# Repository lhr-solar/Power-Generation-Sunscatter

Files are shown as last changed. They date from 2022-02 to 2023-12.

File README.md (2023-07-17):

# :sunny: Sunscatter - Maximum Power Point Tracker Board

- [:sunny: Sunscatter - Maximum Power Point Tracker Board](#sunny-sunscatter---maximum-power-point-tracker-board)
  - [Repository Structure](#repository-structure)
  - [Maintainers](#maintainers)
  - [Versioning](#versioning)
  - [TODO](#todo)

---

## Repository Structure

- **datasheets** - contains datasheets for major components of the Sunscatter.
- **docs** - contains documentation on how to build, test, and use the Sunscatter.
- **fw** - contains fw that is loaded onto the Sunscatter.
  - **tests** - test programs used to characterize and validate the Sunscatter.
  - **src** - main program used to run the Sunscatter.
  - **inc** - internally developed libraries specific for the Sunscatter.
  - **lib** - third party libraries used by the Sunscatter.
- **hw**
  - **Footprints** - project specfic footprint association files for the Sunscatter.
  - **Models** - 3d .step files for the PCB 3d viewer.
  - **Symbols** - project specific symbol files for the Sunscatter.
  - **vX_Y_Z** - frozen versioning folder for PCB production files.
  - design files

---

## Maintainers

The current maintainer of this project is Matthew Yu as of 07/16/2023. His email
is [matthewjkyu@gmail.com](matthewjkyu@gmail.com).

Contributors to the HW and FW encompass many dedicated students, including:

- Jacob Pustilnik
- Afnan Mir
- Youssef Elsherif
- Austin Tsao
- Joseph Onofre
- Ricky Tiet
- Javier Lopez
- Chioma Okorie
- Corey Hulse
- Kaleb Todd
- Jennifer Dahm
- And many others...

Special thanks to Professor Gary Hallock, who supervised the development and
design of this project.

---

## Versioning

This PCB is on unified version `3.4.0`. Every time the schematic and/or layout
is updated, this version number should go up. We use [semantic
versioning](https://semver.org/) to denote between versions. See the
[changelog](./docs/CHANGELOG.md) for more details.

---

## TODO

Documentation

- Update assembly and testing document, ordering document, and improvement document.
- Add datasheets for key components of the device.

HW

- Transition to v4.0.0 using modified board design from MPPT-design repo
- Clean up files in hw folder

SW

- Regenerate code for MBED with proposed filestructure

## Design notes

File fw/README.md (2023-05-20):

# Sunscatter Firmware

This repository contains all relevant firmware and documentation files for the
Sunscatter MPPT FW.

A couple other important sections for programmers who are working with this
board are below. 

- [Repository Structure](#Repository-Structure)
- [Maintainers](#Maintainers)
- [Versioning](#Versioning)
- [Changes and Errata](#Changes-and-Errata)
- [List of TODOs](#TODO)

---

## Repository Structure
- **inc**: Includes additional files and libraries made by external sources,
  like MBED from ARM.
- **lib**: Includes additional files and libraries developed by internal sources.
- **src**: Includes all projects, including test programs. The main program is
  typicalnamed after the root directory name. E.g. Sunscatter.
- **documentation**: Contains documentation for building, flashing, testing, and
  characterizing the HW.
  - [IMPROVEMENT.md](documentation/IMPROVEMENT.md): Suggestions for improving
    the software, libraries, and/or tests.
  - [BUILDING.md](documentation/BUILDING.md): Instructions for installing all
    prerequisites and building the program. Also how to flash onto the board.
  - [TESTING.md](documentation/TESTING.md): Instructions for testing the board
    hardware (past the basic electrical tests found in
    pcb/documentation/ASSEMBLY_AND_TESTING.md) and characterizing the hardware. 

---

## Maintainers

The current maintainer of this project is Matthew Yu as of 07/15/2022. His email
is [matthewjkyu@gmail.com](matthewjkyu@gmail.com). 

Also a useful point of contact is Professor Gary Hallock, who advised Matthew
and worked with the several former senior design teams and solar car class
groups who developed this board.

Other contributors of this FW are as follows:
- Afnan Mir (v0.1.0)
- Roy Moore (v0.1.0)
- Gary Hallock (v0.1.0)
- And many others...

---

## Versioning

Each FW program has an internal version number located at the header. The
current FW version of the main program, `MPPT` is `0.1.0`. It is still in beta.
We use [semantic versioning](https://semver.org/) to denote between versions.

---

## Changes and Errata

### Release 0.1.0

- Initial formatting of the repository structure
- Added the following tests:
  - boost_characterization_test
  - can_test
  - indicator_test
  - sensor_test
  - step_response_test
  - voltage_sweep_mppt_test
- Added main program Sunscatter.
- Versioning for each test based on hardware revision.

---

## TODO
- [#1. Figure out switching node requirements on overshoot and ringing.](https://github.com/lhr-solar/Power-Generation/issues/1) 
- Add libraries for Sunscatter program.
- Update Sunscatter program to use on MPPT.
- Clean up Boost Characterization Test.

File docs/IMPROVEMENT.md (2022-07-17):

# IMPROVEMENTS FOR SUNSCATTER HW

v1.0.0

This is a list of changes we can make to the board in future versions to improve
it in various ways. Some of these are functional, others are purely aesthetic.

1. **Isolate Nucleo From High-Power Domain**

   Currently, the Nucleo operates in the same power domain (that is, the same
   ground and without isolation) as the high power components of the board -
   that is, the DC/DC boost converter. It would be far safer for it to be
   isolated, both for the Nucleo itself and for users interacting with it.

   Once the Nucleo is properly isolated from the high-power domain, it can
   either be tied directly to the car's low-power domain, or it can remain
   isolated from it. For simplicity I recommend tying it to the car's low-power
   domain, but it might be slightly safer for operators if it's isolated.

   Three major components would need to be reworked to enable this:
   1. the voltage sensors
   2. the current sensors
   3. the MOSFET driver

   These are the next couple of numbered points.

2. **Upgrading the voltage sensors**

   To upgrade the voltage sensors, we would want to use an isolating amplifier
   such as the AMC1211. This chip has an input range of 0-2V, so we would need
   to adjust the voltage dividers and their protection diodes appropriately.
   Both the input and the output require 3.3-5V power.

   The output of TI's isolating amplifiers, unfortunately, is differential
   rather than single-sided. (Explain how to convert this. example in
   datasheet. Idea: difference amplifier like INA132?)

3. **Upgrading the current sensors**

   Just like voltage sensors, but with current-sense isolating amplifiers.

4. **Upgrading the MOSFET driver**

   This is a fairly easy upgrade, since our current chip already looks a lot
   like an isolated FET driver.

   TI designs chips specifically for driving MOSFETs through isolation. One
   example of this is the UCC21541, with dual-channel isolation.* On the
   input/Nucleo side, you would provide 3.3V power from the Nucleo and use
   standard IO to drive IN_A. On the output side, you would provide 12V from the
   high-power domain and route the output just like you would from our current
   chip.

   As of this writing, the price for the UCC21541 is similar to that of our
   current chip, but Mouser currently doesn't stock it. We would want to find
   one that operates similarly but that Mouser actually stocks.

   We only need one channel, but the only chips TI offers with one-channel
   isolation are far more complicated to use.

5. **Switch to synchronous boost converter**

   Up to 8A * 1.75V = 14W may be dissipated through the schottky diode forward
   bias mode. Perhaps higher based on surge current. This loss can be reduced by
   replacing the schottky diodes with low Rds_ON mosfets. This may also reduce
   the need for a third heatsink.

   Note that the noise should proportionally double. We should test combinations
   of the boost converter with the snubber circuit to see if the power loss
   through the snubber is more significant than the power saved using a
   synchronous topology.

6. **Add ports for light and temperature sensors**

    Merging the Blackbody boards with Sunscatter can reduce board waste for
    minimal space utilization. Required: 2 TSL2591 or equivalent light sensing
    ports, and up to 8 RTD sensors. The latter may use a multiplexer and a
    single MAX31865 chip. Test w/ v2.0.0 of Blackbody A first.

7. **Upgrade MCU processor and use just the chip**

    Currently we use the nucleo breakout board. Other LHR Solar boards solder
    the STM32L432KC chip directly to the PCB. This reduces space and removes
    extra peripherals that are not used. Requires extra hardware for STLINK
    communication and flashing.

8. **Reset switch Pullup**

    Powering the Nucleo through 5V (using Car Power 12V instead of the 9V supply
    for testing) needs a pullup resistor on the reset switch (SW101). Behavior
    is finnicky and the Nucleo onboard pullup is insufficient.

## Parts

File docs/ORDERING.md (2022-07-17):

# HOW TO ORDER THIS PCB

v1.1.0

Ordering the board will vary from distributor to distributor; some will take the
KiCAD project directly, others require Gerber files. If they require gerber
files, some will require specific naming conventions for each layer.

## Ordering Instructions: JLCPCB

Our preferred manufacturer (or at least mine) of choice is JLCPCB. They
manufacture hobby boards cheaply and quickly, and at relatively high quality
compared to other fab houses.

JLCPCB will manufacture 5 PCBs for 2$ (sans shipping and handling) if the PCBs
are <= 100mm * 100mm. They also have an SMD assembly surface where one side of
the PCB is populated, often for very cheap prices compared to the amount of
labor you would have to put in to solder all the components on.

For this PCB (Sunscatter), we will order from JLCPCB and also do SMD assembly
from them. KiCAD has nice, open source extensions that can quickly create build
files that JLCPCB will accept for manufacturing and assembly.

### Preparing the Gerbers

First make sure that the JLCPCB plugin is installed via the Plugin and Content
Manager.

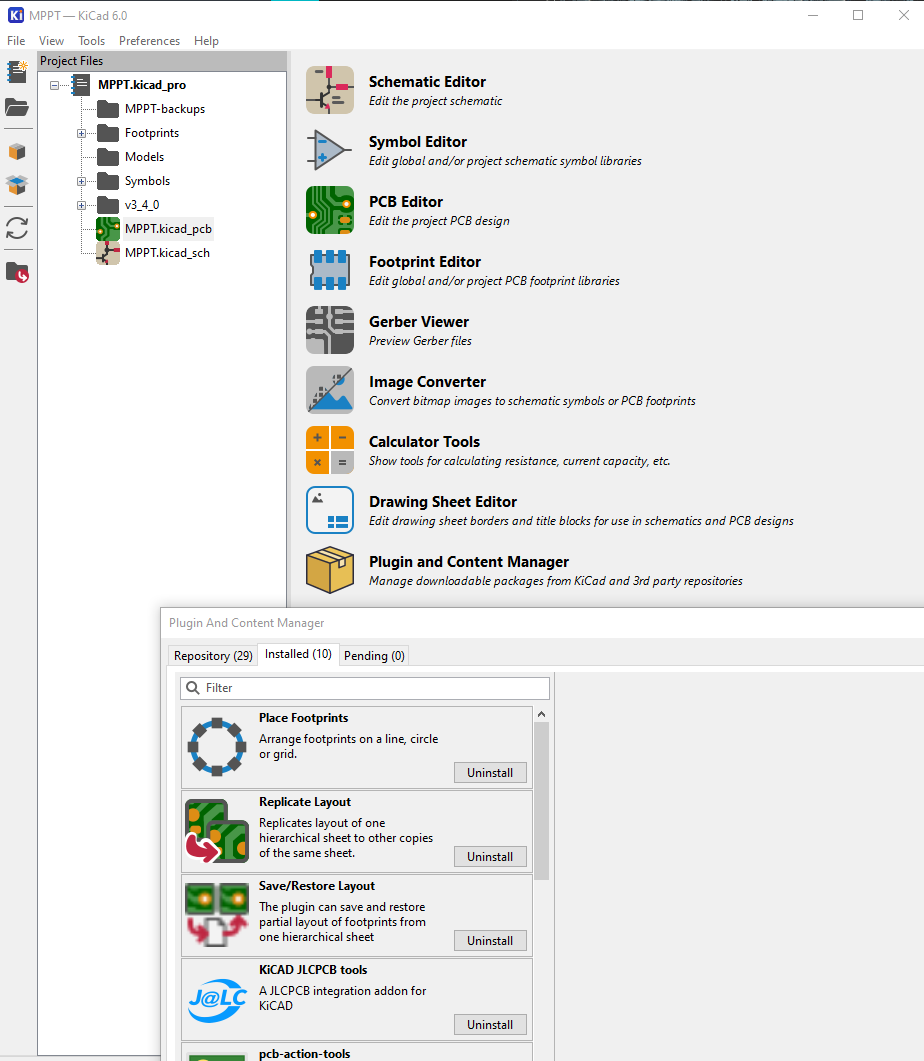
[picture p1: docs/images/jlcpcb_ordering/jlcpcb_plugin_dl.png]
Install plugin


Then make sure your schematic symbol table has following columns populated for
each component:
- Value
- Reference
- Footprint
- JLCPCB BOM
- LCSC Part

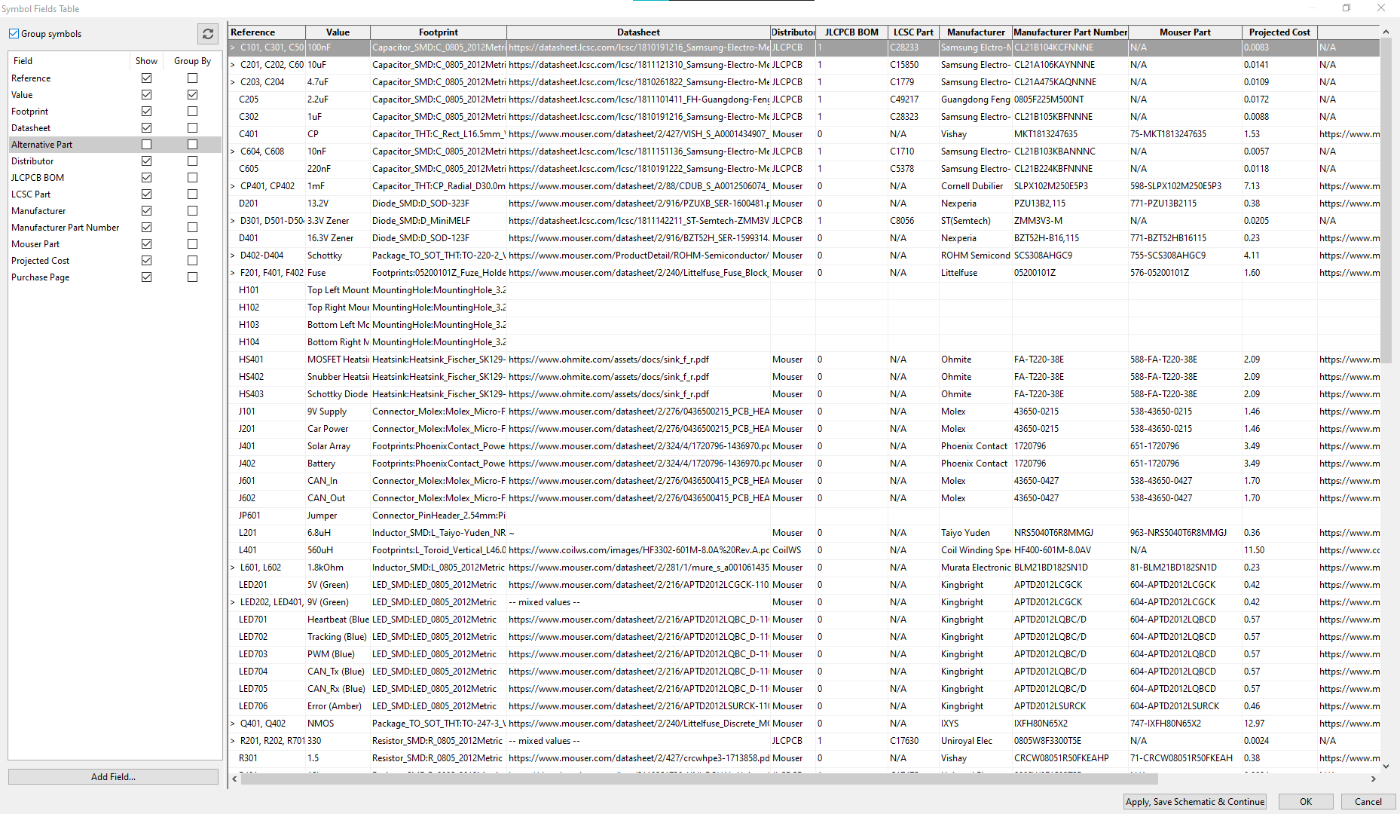
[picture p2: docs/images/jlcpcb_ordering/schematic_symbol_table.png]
Populated symbol table


Go to the PCB editor, and after the layout finishes and everything passes DRC
click on the JLCPCB button.

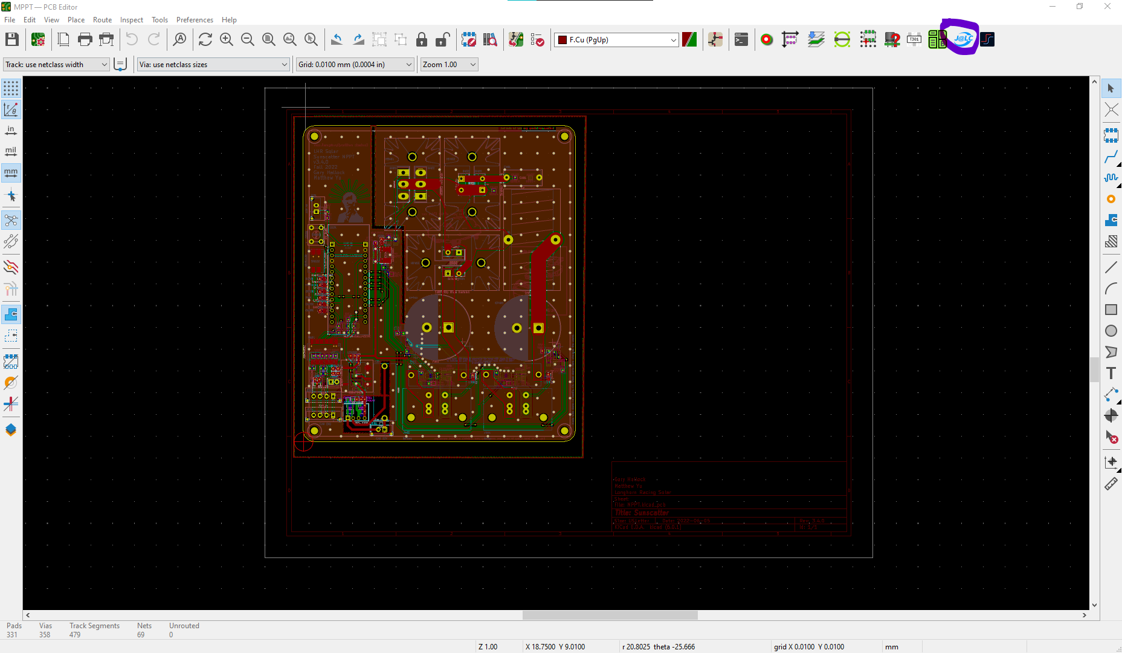
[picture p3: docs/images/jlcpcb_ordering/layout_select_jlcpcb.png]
JLCPCB buttom


Finally generate the fab files using the Generate Fabrication Files button. Make
sure the BOM and POS have a checkmark for all components you want assembled by JLCPCB.

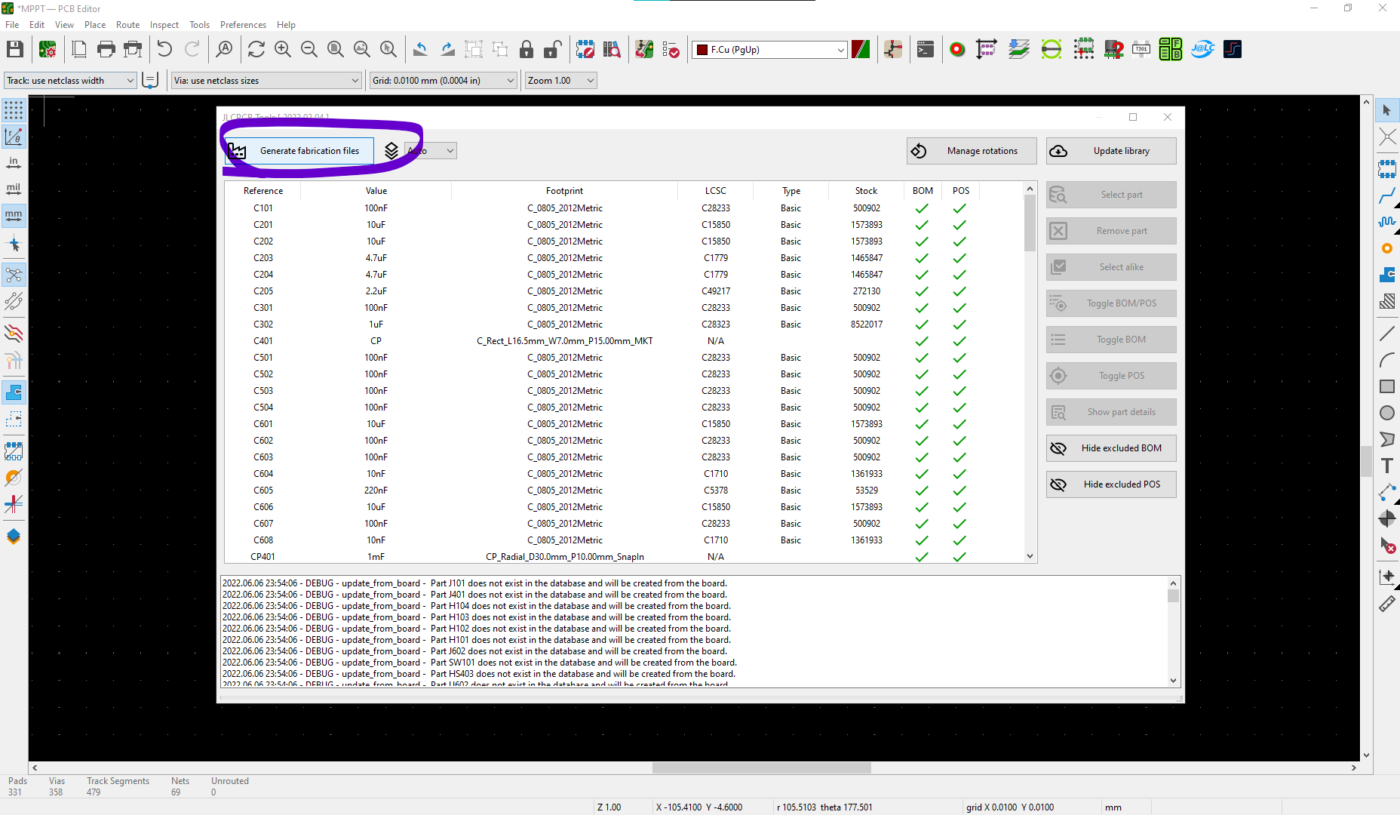
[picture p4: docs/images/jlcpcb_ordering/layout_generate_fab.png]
Generate gerbers


### Ordering from JLCPCB

After the gerbers are generated properly, head onto the JLCPCB
[site](jlcpcb.com).

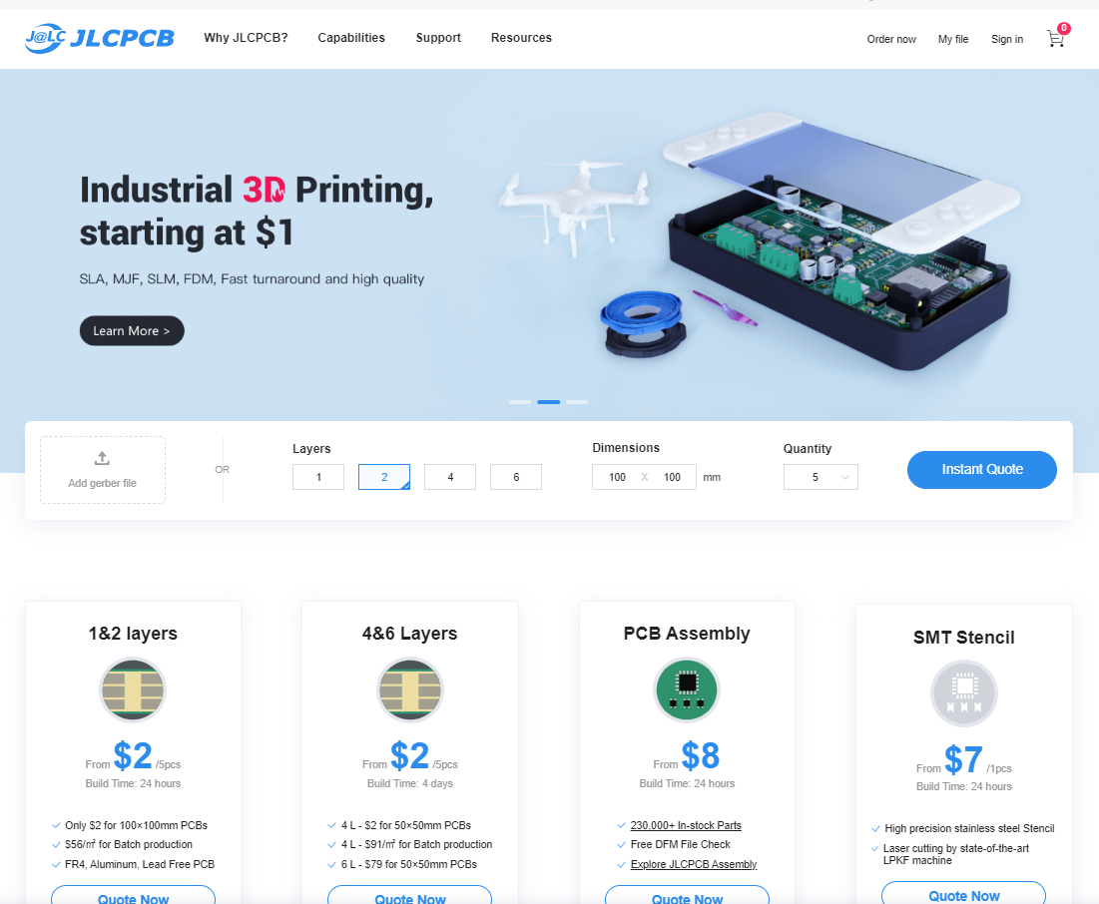
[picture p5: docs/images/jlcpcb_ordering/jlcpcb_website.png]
JLCPCB site


Go and get a quote.

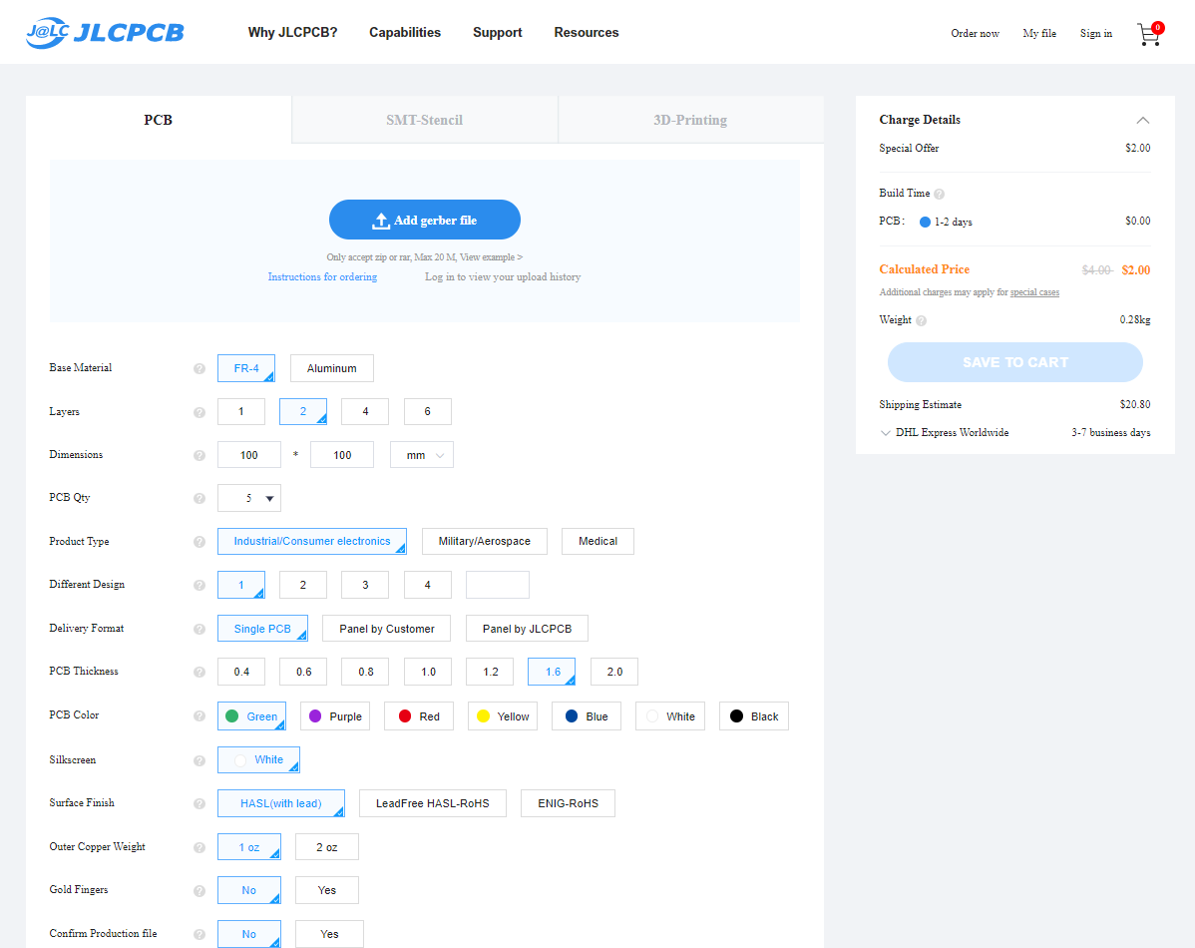
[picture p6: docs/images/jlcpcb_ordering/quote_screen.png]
JLCPCB quote


If you press the add gerber file button, you can upload the output gerber files.
They are found in the `jlcpcb/assembly/gerber` folder as `GERBER-xxx.zip`.

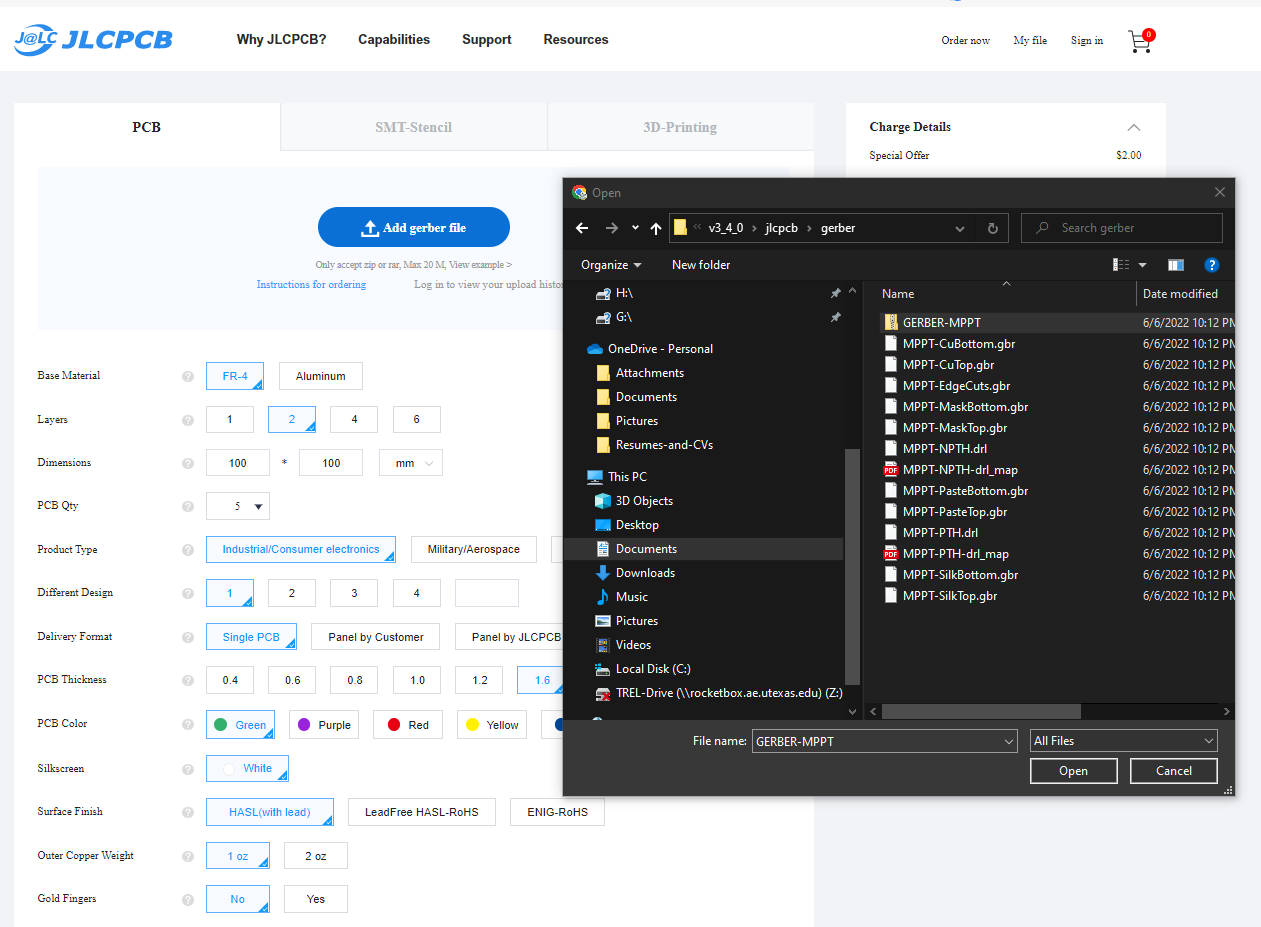
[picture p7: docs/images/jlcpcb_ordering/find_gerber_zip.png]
Adding gerbers


The webpage will load the gerbers, if they are in the correct format and board
passes some checks it'll show up. The dimensions of the board will be updated
and a new quote price will be displayed.

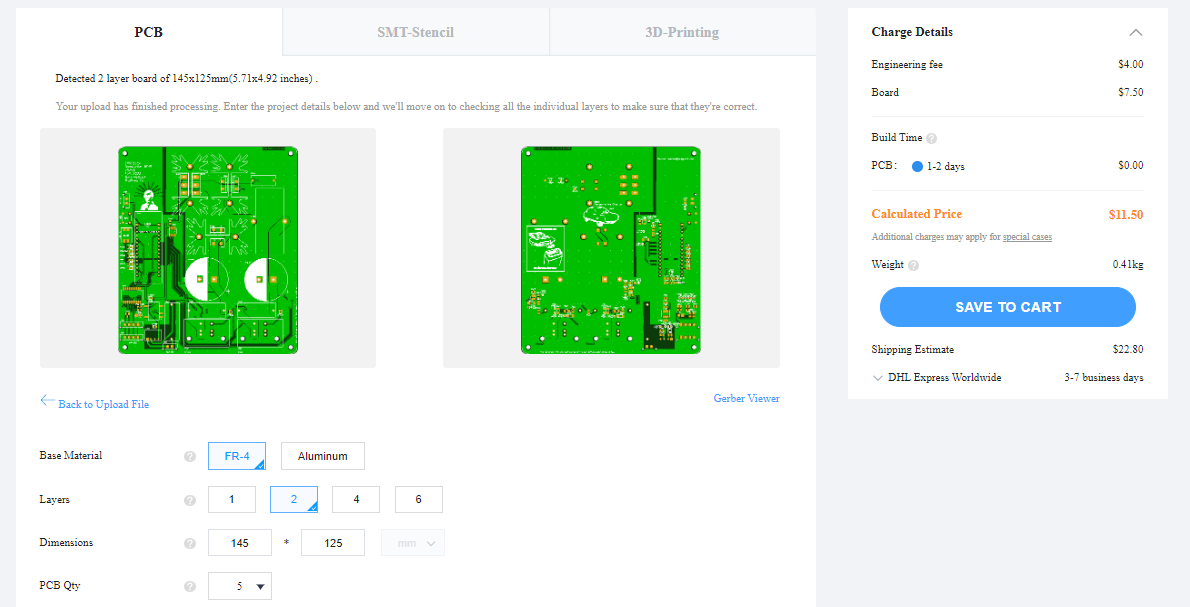
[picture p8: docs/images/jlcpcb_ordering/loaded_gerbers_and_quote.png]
New quote


We can then go down the screen and enable the PCB assembly option. We can choose
which side we want to assemble and the number of boards to assemble (2 or 5).

Assembly option

The next page after hitting confirm asks for a BOM and CPL file, the latter is
the position of the components to be assembled on the board. We can find those
as `jlcpcb/assembly/BOM-xxx.csv` and `jlcpcb/assembly/POS-xxx.csv` respectively.

Assembly file input

The next page will load the BOM and check against the LCSC internal database and
match all available components. We prefer basic components since every extended
component is an extra 2$ fee per type to manually load.

BOM matching

The next page reviews the PCB, you can zoom in on the screen to see where each
component will be placed. Make sure it matches or the engineer who inspects the
files will send an email back with complaints and the order will be delayed.

Review
Zoomed in

Finally you can save the order to the cart, review everything, and order it.
Feel free to select the delivery system that best fits your timeline and the
budget, and use any coupons if you have any.

Shopping Cart

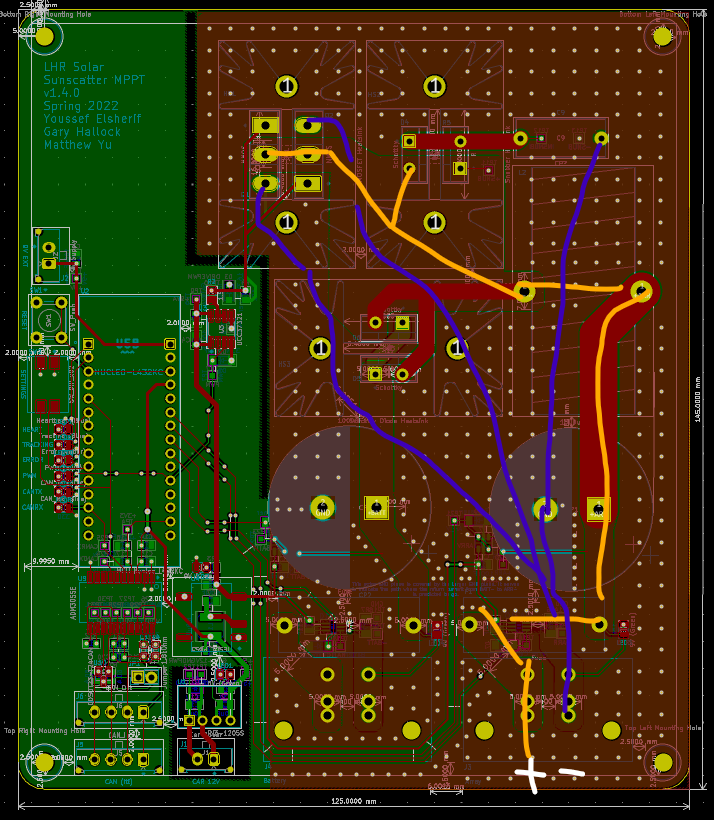
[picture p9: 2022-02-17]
docs/images/jlcpcb_ordering/GateON.png

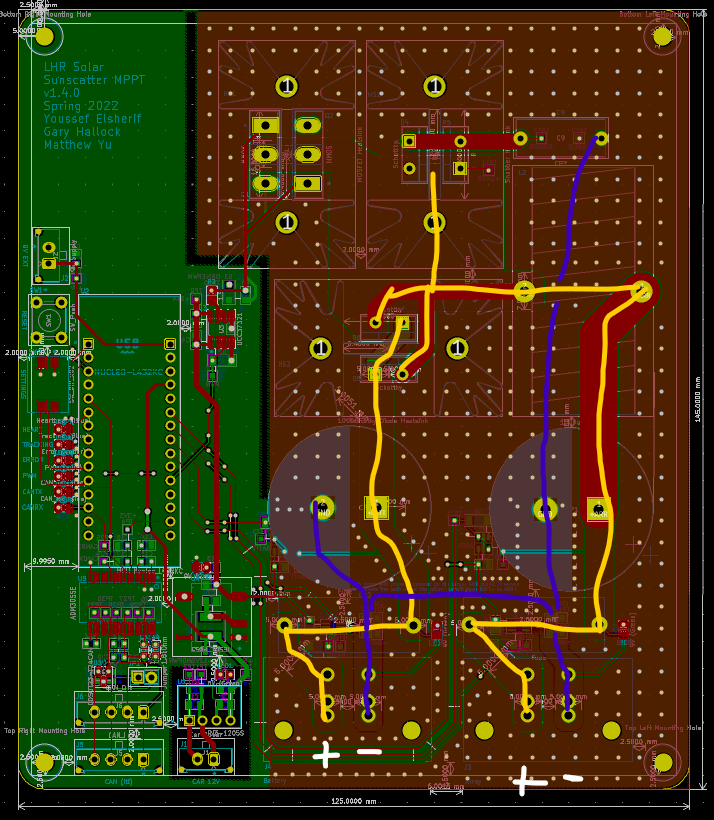
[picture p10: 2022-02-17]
docs/images/jlcpcb_ordering/GateOFF.png

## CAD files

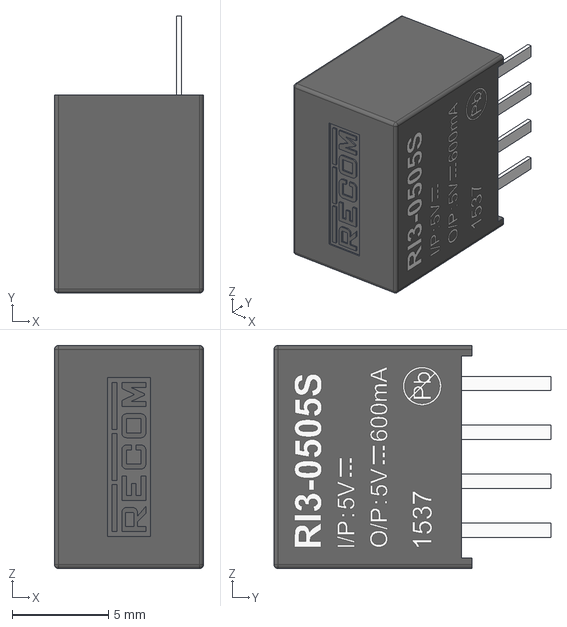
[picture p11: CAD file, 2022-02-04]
hw/Models/RI3-1205S.step
7.75 x 14.4 x 11.6 mm

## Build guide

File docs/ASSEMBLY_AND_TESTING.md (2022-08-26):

# HOW TO ASSEMBLE AND ELECTRICALLY TEST THIS PCB

v1.1.0

## Assembly and Testing Instructions

### v3.2.0

The board should be assembled and tested in sections to ensure proper
functioning. Assembly should go through the following sections in order:

1. Power Regulation
2. LEDs
3. Nucleo Connections
4. Sensors (Voltage and Current)
5. CAN
6. DC/DC Converter

#### Step by Step Instructions

It's highly recommended to pull up the schematic and layout side by side while
assembling and testing the board. As a tip, you can click on the schematic
symbol, and if the layout window is open, it'll jump to that part on the layout.
Also hide everything except the Silkscreen or Fabrication layer (of the right
side of the PCB) to remove any clutter from the layout.

Also, if you find any discrepancies between these instructions and the board
layout, please file a PR or issue so it can be fixed!

1. Initial Board Checks

   Before installing anything, check for power shorts where there shouldn't be:
   - Between Array + and -
   - Between Battery + and -
   - Between Array and Battery
   - Between Car Power +12V and GNDPWR
   - Between Device Power +9VA and GNDREF
   - Between Car Power +12V and Device Power +9VA
   - Between Car Power GNDPWR and Device Power GNDREF
   - Between CAN Iso Vout and GndOut
   - Between CAN Iso Vin and GndIn
   - Between CAN Iso Vout and Vin
   - Between CAN Iso GndOut and GndIn

   Other important shorts to check for and eliminate:
   - Between CAN H and L
   - Between MOSFET terminals
   - Between Schottky Diode terminals
   - Between heat sinks and ground
   - On each Nucleo board, between A4 and D4 (shorted by SB18)
   - On each Nucleo board, between A5 and D5 (shorted by SB16)

2. Assembling Power Regulation

   1. Solder the smallest components first: L1, C4, C5, C6, C7. These can be
      done in any order.
   2. Solder test points: TP5, TP6, TP7, TP8. These can be done in any order.
   3. Solder power regulator U3.
   4. Solder the connector J1.
   5. Test for the following shorts:
      - Between Car Power +12V and GNDPWR.
      - Between Device Power +9VA and GNDREF.
      - Between Car Power +12V and Device Power +9VA.
      - Between Car Power GNDPWR and Device Power GNDREF.
      - Between pins on U3
   6. Connect +12V to the connector and verify that +9VA is at TP7.
   7. As a bonus, somehow make some noise at +12V and see how stable +9VA is.

3. LEDs

   1. Solder the smallest components first: R2 - R11 and LED1 - LED10. You get
      the drill by now.
   2. Check for shorts across each resistor-LED pair. As a tip, the LED
      reference number is always one less than the resistor reference number.
   3. Further testing on these will occur in the next step.

4. Nucleo Connections

   1. Solder the smallest components first: D1, D2, C1, C2, C3, R1. Make sure
      you know which direction the diodes should go on the layout. You get the
      drill by now.
   2. Solder test points: TP1, TP2, TP3, TP4.
   3. Solder the Drive PWM signal driver U2.
   4. Solder the headers for the Nucleo (U1) and make sure they are upright.
   5. Then solder in the switches SW1 and SW2.
   6. Test for the following shorts:
      - Across SW1 (shorts only when pushed)
      - Across SW2 (shorts only when ON)
      - Between pins on U2 (and U1, if you're bored)
   7. Plug in the Nucleo and then test for shorts between D4 and A4 and between
      D5 and A5. If there are shorts here, you will need to remove SB18 or SB16,
      respectively, from the Nucleo board.

      **YOU MUST DO THIS FOR EVERY NUCLEO YOU PLUG INTO THE MPPT.**

   8. Load up the Nucelo with a test program to cycle LED pins and outputs a PWM
      signal with a non-trivial duty cycle and see if they light up/are correct
      on an O-scope. Unplug the Nucleo from USB, and connect 12V to the Car
      Power Connector J1 (But not both!). Make sure the Nucleo powers on again
      and the test program works as expected.
   9. Remove the Nucleo and all sources of power before further assembly.

5. Sensors (Voltage and Current Sensors)

   It's recommended to do one of these sensors at a time.

   1. Pick a sensor. We'll use the Array Voltage Sensor as an example.
   2. Solder the smallest components first: R18, R19, R20, C15, D11, D12. Make
      sure you know which direction the diodes should go on the layout.
   3. Solder test point TP19.
   4. Solder the chip U6.
   5. Test for shorts across the pins on U6, and that we have a connection
      between pad 6 of U6 (+3.3V) and the +3.3V pin of the Nucleo (after
      plugging it in, but not powering it).
   6. To test the sensor, you can now power the Nucleo with the USB.
      Apply a large voltage across Array +/- (likewise with Battery +/-). The
      LED circuitry for the array is designed for up to 100V, and the LED circuitry
      for the battery is designed for up to 130V.

      Note: If you're starting with the voltage sensors, you'll need to bridge
      Arr- or Batt- with GNDPWR first until the current sensors are installed.
      You could probably do a solder bridge on the current sensor shunt
      resistor, but if you're uncomfortable removing solder there later, use
      some thick wire to bridge the test points for ARR- (TP12) and BATT- (TP16)
      with the GNDREF test point (TP8). You could also use -SNUB (TP15) as
      GNDREF.

      Make sure you can read the expected voltage or voltage range at the output
      test points. You might also want to run a profile across the sensors and
      profile the relationship for interfacing the sensors in SW later. At
      least, it'll make your life easier in the future.

      Make sure you remove the Nucleo and any power after testing.

6. CAN Circuit

   1. Solder chip U8 **first** and test for shorts across adjacent pins.
   2. Solder the smallest components: C17 - C24, L3, L4, R25, R26.
   3. Solder bridge R24.
   4. Solder test points TP21 - TP28.
   5. Solder the chip U9.
   6. Solder the termination header JP1.
   7. Solder the CAN Connectors J4, J5.
   8. Test for the following shorts:
      - Between CAN_H and CAN_L.
      - Between CAN_Tx, CAN_Rx.
      - +5V and GNDPWR (Power side).
      - 5V and GND (CAN side).
      - Across adjacent pins in U8, U9.
   9. Plug in the Nucleo, connect J4/J5 to a CAN bus, and run a CAN
      communication test to ensure that the installed CAN circuitry is
      functional.
   10. Remove any power, the Nucleo, and then CAN connections before further
       assembly.

7. DC-DC Converter
   1. Solder the smallest components first: D3, R12. Make sure you know which
      direction the diodes should go on the layout.
   2. Then do some of the larger parts, in no particular order: F1, F2, R13, C9.
   3. Now install the heatsinks HS1 - HS3.
   4. Then install the MOSFETs and other diodes: Q1, Q2, D4, D5, D6. Make sure
      they fit the heatsinks and have a screw inserted to keep them connected.
      Maybe add thermal paste.
   5. Install the test points: TP9 - TP16.
   6. Finally, install the large stuff: J2, J3, C8, C9, L2.

8. Post checks

   Now that you've made it to the end (we hope) of assembly and preliminary
   testing, you should do a couple things before running full MPPT tests and
   running MPPT algorithms on it.

   1. First, check the board for obvious soldering defections like burnt traces
      or exposed component legs. Make sure those still work. For any solder
      bridges that shouldn't fix, you should fix them. Or get somebody who's
      better than you to fix them.
   2. Check to see if you have any remaining parts hiding in the pile of
      plastic packages you probably received. Any remaining parts should
      probably be a cause for concern (unless you knew you were going to blow
      something and had the foresight to get extra) and you should definitely
      see where they might have come from.

      The MPPT Parts list is **THE** definite source of truth, and tells you
      where each part is tied to which reference and thus their position on the
      layout. Check there first before running to the electrical lead to help
      you.
   3. It might be a good idea if you're bored to run any electrical/short tests
      that were described earlier in these instructions. There's always a small
      chance that some assembly you did later on broke/removed/damaged previous
      parts.

### v3.3.x, v3.4.0

> v3.3.x should be compatible with these instructions, although component
> numbering will be different.

The board should be assembled and tested in sections to ensure proper
functioning. Assembly should go through the following sections in order:

1. Pre Board Checks
2. Power Regulation
3. MCU
4. LEDs
5. CAN Driver
6. Gate Driver
7. Sensors
8. DC/DC Converter
9. Post Board Check

#### Step by Step Instructions

It's highly recommended to pull up the schematic and layout side by side while
assembling and testing the board. As a tip, you can click on the schematic
symbol, and if the layout window is open, it'll jump to that part on the layout.
Also hide everything except the Silkscreen or Fabrication layer (of the right
side of the PCB) to remove any clutter from the layout. You can also use the
provided `ibom.html` (open it in your browser!) for placing components. This is
useful for tracking assembly.

Ideally, JLCPCB or the PCB manufacturer will have assembled most of the board,
if not just the passives. For the components that are already on the board, you
do not need to solder them on, but make sure to test them!

Also, if you find any discrepancies between these instructions and the board
layout, please file a PR or issue so it can be fixed!

##### Soldering Order
1. The recommended order for soldering components are:

    1. Soldering the smallest components.
    2. Solder from the center outwards.
    3. Soldering the back side components.
    4. Soldering the SMD components.
    5. Soldering the through hole components.

    An example of this priority system is soldering on the LEDs (LED201,
    LED202) and the SMD converter (U202) prior to the Molex connector (J201)
    and the fuse box (F201).

##### Testing Instructions
1. Pre Board Checks

    Before installing anything, check for power shorts where there shouldn't be.
    This list is not exhaustive, and only consist of either power lines or high
    energy signals that cannot be current limited by the source.
    - Power Regulation
        - __F201 Fuse:__ +12V (J201 Pin1) and +12V (TP201)
        - __12V Car Power Line:__ 12V (TP201) and Car GND (TP202)
        - __+5V Board Power Line:__ +5V (TP204) and Board GND (TP203)
        - __9VA Board Power Line:__ 9VA (TP205) and Board GND (TP203)
        - __12V to +5V Transition:__ 12V (TP201) and +5V (TP204)
        - __+5V to 9VA Transition:__ +5V (TP204) and 9VA (TP205)
        - __Car to Board Isolation:__ Car GND (TP202) and Board GND (TP203)
        - __+3V3 Board Power Line:__ +3V3 (TP101) and Board GND (TP203)
    - DC/DC Converter
        - __F401 Fuse:__ Solar Array+ (J401 Pin1) and +ARR (TP507)
        - __F402 Fuse:__ Battery+ (J402 Pin1) and +BATT (TP509)
        - __+ARR Power Line:__ +ARR (TP507) and -ARR (TP502)
        - __+BATT Power Line:__ +BATT (TP509) and -BATT (TP505)
        - __Drive PWM Isolation:__ GATE (TP401) and Board GND (TP203)
        - __Snubber Isolation:__ +SNUB (TP402) and -SNUB (TP404)

        Note that -SNUB (TP404), GND (TP203, TP302, TP501, TP505) are functionally equivalent.

2. Power Regulation

    Following the soldering order, solder on the components specified in the
    power_regulation schematic page (ID: 2/7).

    To test this circuit, after soldering, insert an 8A fuse into the fuse
    holder (F201) and plug into the molex connector (J201) a 10.8 - 13.2 VDC
    source.

    Using a multimeter, measure across 12V (TP201) and Car GND (TP202). This
    should be the value of your input. The output of U201 at +5V (TP204) and
    Board GND (TP203) should be 5V. The output of U202 at 9VA (TP205) and Board
    GND (TP203) should be 9V.

    Additionally, the LEDs (LED201, LED202) should both be on and green.

3. MCU

    Following the soldering order, solder on the components specified in the
    root schematic page (ID: 1/7). The Nucleo should be plugged into standard
    2.54mm headers that are soldered into the U101 footprint so they can be
    replaced if necessary.

    To test this circuit, after soldering, plug in the molex connector (J101) a
    7 - 12 VDC source.

    Using a multimeter, measure across +9V (TP102) and Board GND (TP203). This
    should be the value of your input. The output of U101 at +3V3 should be
    3.3V.

    Additionally, the onboard LED of the Nucleo should turn on when powered.

    Additionally, the reset switch (SW101) should turn off the onboard LED when
    held down. This should happen when the Nucleo is powered through the 9V
    supply (J101) or when Car Power is applied (J201).

4. LEDs

    Following the soldering order, solder on the components specified in the
    leds schematic page (ID: 7/7).

    Apply voltage across the circuits (input and GND). The LEDs should turn on
    if the polarity is correct.

    Additionally, run the indicator_test from the Power-Generation/Sunscatter
    fw. The LEDs should turn on and off in a round-robin order.

5. CAN Driver

    Following the soldering order, solder on the components specified in the
    can_driver schematic page (ID: 6/7).

    Run the can_test from the Power-Generation/Sunscatter fw with another CAN
    capable (and working!) board. One board should be specified as
    `__USER_ONE__` and the other should not be. This test should pass a message
    between the two boards every second and should be visible on a serial
    terminal (115200 baud).

6. Gate Driver

    Following the soldering order, solder on the components specified in the
    gate_driver schematic page (ID: 3/7). 

    +3V3 using a F-M jumper can be routed from a powered Nucleo to the PWM pin
    (TP301). Based on the driver populated (UCC37322, noninverting), (UC37321,
    inverting), the output should be ~8.5-9V based on the input state (0, 3.3V).
    This can be measured from the Gate testpoint (TP401) and -SNUB (TP404).

7. Sensors

    Following the soldering order, solder on the components specified in the
    sensor schematic page (ID: 5/7).

    To test but not calibrate these sensors (a whole another topic, see the
    Power-Generation/Sunscatter/test_data/sunscatter_characterization/sunscatter_characterization.xlsx
    spreadsheet for more details), power the board (+9VA LED should light up).

    Using a power supply, apply some amount of voltage across the voltage
    sensors with the +ARR or +BATT connectors. Use a multimeter to measure the
    op amp output at TP508, TP510. This should match the given voltage divider
    ratio output.

    You can also attempt shorting the +BATT side with the DC/DC converter once
    it is populated and have the GATE open. The current should flow through both
    current sensors (make sure you're current limited to less than 6A! The board
    is theoretically rated up to 8A).

8. DC/DC Converter

    Following the soldering order, solder on the components specified in the
    boost_converter schematic page (ID: 4/7). Apply thermal paste to the
    components that will be attached to the heatsinks, screw them into the
    heatsinks, _and then_ insert them into the board for soldering.

    To test but not calibrate the converter (a whole another topic, see
    Power-Generation/Sunscatter/test_data/dc_dc_converter_characterization/ for
    more details), power the board (+9VA LED should light up).

    Stick an oscilloscope probe across the snubber (TP402, TP404) and on the
    output (TP509, TP404). Input a fixed power source (perhaps 10V, 1A) at the
    solar array connector and attach a signal generator to the GATE (TP401,
    TP404). Observe the voltage output and the snubber/output waveforms as the
    signal generator waveform (recommend square wave) frequency increases.

9. Post Board Check

    1. Check the board for obvious soldering defections like burnt traces
       or exposed component legs. Make sure those still work. Remove any solder
       bridges and use q-tips dipped in isopropyl alcohol or flux remover to
       clean away any flux used during assembly.
    2. Make sure that there are no parts remaining that have not been assembled
       (excluding spares). The ibom.html mentioned earlier can be helpful for
       this.
    3. The parts list embedded into the KiCAD project, the ibom.html, and any
       boms generated are the source of truth for the PCB. If there are any
       inconsistencies between the three or with your assembly, make sure you
       correct the inconsistency or file an issue so it can be fixed.
    4. Feel free to fall back on running the tests described here to do sanity
       tests when the PCB stops working or exhibits undefined behavior. Assembly
       and/or usage may break or damage the circuit, even if you think you were
       careful with it.

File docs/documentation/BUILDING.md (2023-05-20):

# BUILDING THIS PROGRAM AND FLASHING TO THE PCB

v1.0.0

## Prerequisites

When first initializing this repo, please make sure the `mbed-os` library is in
`inc`. The current version is `6.15.1`. [Mbed
Studio](https://os.mbed.com/studio/) should also be installed.

## Building

When building this project, switch the open workspace to `src`. Mbed Studio will
not recognize that the projects exist without the program folder being at the
root of the workspace.

The appropriate target is the `NUCLEO-L432KC`. This is autopopulated if the
nucleo is plugged into the PC via a USB cable. On the first build, the compile
time will take a while.

An `mbed_app.json` can be added to the program folder. Additional options can be
specified, such as the UART baud rate or the printf precision. See the provided
`mbed_app.json` file in the src subfolders for details.

## Viewing UART/virtual COM serial output

Assuming the HW has the correct UART peripheral pins available to talk via the
USB-UART chip, Mbed Studio has a built in serial monitor for viewing any debug
output.

It is preferred to use PuTTy or a custom serial viewer, however, since the
serial monitor in Mbed Studio may time out after a certain amount of lines.

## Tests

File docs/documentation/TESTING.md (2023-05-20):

# HOW TO TEST AND CHARACTERIZE THE HARDWARE

v1.0.0

## Testing instructions

In addition to the main, defined in `src/Sunscatter`, several test and
characterization programs have been created. They are noted briefly here.

- **Indicator Test**: tests LEDs on Sunscatter PCB.
- **CAN Test**: tests CAN peripheral and HW on Sunscatter PCB.
- **Sensor Test**: tests sensor HW and sensor calibration on Sunscatter PCB.
- **Step Response Test**: characterizes the transients for voltage and current
  across the DC-DC converter on the Sunscatter PCB.
- **(*UNDER CONSTRUCTION*)** **Boost Characterization Test**: Characterizes unloaded
  and loaded boost parameters of the DC-DC converter.
- **(*USE FOR ARRAY TESTING*)** **Voltage Sweep MPPT Test**: sweeps across the input
  source and sets a reference 
  at the PWM duty cycle that maximizes either efficiency or power transmission.
- **(*UNDER CONSTRUCTION*)** **Sunscatter**: main program for the Sunscatter PCB.

After building each program and loading them onto the Nucleo, the testing
instructions are as follows. 

---

### Indicator Test

Observe that each LED on the board not controlled by the presence of power
toggles in some sequence. This includes the onboard Nucleo LED. 

---

### CAN Test

Hook up the CAN circuitry with another PCB using the same CAN circuit. Make sure
CANH and CANL are connected to CANH and CANL, respectively. Make sure one device
is flashed with `__USER_ONE__` defined and the other without. This can be done
by commenting out the line `#define __USER_ONE__ 0`. 

The device with USER ONE defined will send `User 0 sent message <COUNTER>` and
the device with USER ONE undefined will send `User 1 send message COUNTER`. Each
should receive messages from the other with the response `Message received from
<ID>: <COUNTER>`. The counter from each side may be different, but they should
both increase incrementally. 

---

### Sensor Test

Hook up a power supply to the Array connector input of the PCB and determine
transformation functions for each sensor on the PCB. See
`/test_data/sunscatter_characterization/sunscatter_characterization.xlsx` for
detailed examples. 

---

#### Voltage Tuning

Apply voltage from 0 - 125V at the array connector. Leave the battery connector
open circuit. Keep the GATE signal LOW and the MOSFETs open. Measure the voltage
at the array and battery side, both with a high accuracy multimeter (+ARR|GND,
+BATT|GND) and with the internal ADCs. 

Record the values and build a mapping function (this is generally a linear
function with a upper cutoff) relating input voltage to observed measurement.
Make sure the transformation error is less than 1% for most inputs. 

---

#### Current Tuning

Apply current from 0 - 8A at the array connector. Make the battery connector
short circuit. Keep the GATE signal LOW and the MOSFETs open. Measure the
current at the array and battery side, both with a high accuracy multimeter
(-ARR|GND, -BATT|GND) and with the internal ADCs. 

Record the values and build a mapping function (this is generally a linear
function with a upper cutoff) relating input current to observed measurement.
Make sure the transformation error is less than 1% for most inputs. 

---

### Step Response Test

Hook up a power supply to the Array connector input of the PCB and determine the
transient response at the gate (GATE|GND) and across the schottky diodes
(+ARR|GND, +SNUB|-SNUB, +BATT|GND). See
`/test_data/sunscatter_characterization/sunscatter_characterization.xlsx` for
formatting. 

Trigger the PWM signal to drive the DRIVE_PWM signal up and down at a fixed
frequency (5 HZ). Observe the time series of the array and battery voltage to
record the transient response of the switching event, including: 
- rise time (ms)
- overshoot (V/V, % ratio of steady state voltage)
- ringing
- settling time (ms) 

Likewise observe the same transient response at the GATE signal.
Make sure that the overshoot ratio at the GATE is not greater than `TBD%` of the
steady state voltage. See TODO: [#1](https://github.com/lhr-solar/Power-Generation/issues/1). 

---

### Boost Characterization Test

Hook up a power supply to the array connector input of the PCB and vary the
following independent variables over time: 
- Source (max input current, max input voltage)
- Load (no load, x batteries at Y voltage, Z voltage, A voltage...)
- PWM frequency (20 - 30 kHz)
- % Duty cycle (0 - 99%)

Measure the boost ratio (+BATT:+ARR voltage), power transfer value (BATT power),
and power efficiency ratio (BATT power:ARR power). 

The ideal MPPT has a power efficiency ratio and power transfer value as high as
possible with a boost ratio closely at the bounds of the array input range and
battery output range.  

---

### Voltage Sweep MPPT Test

Hook up the array or power supply to the array connector and a load the output.
It should perform a successful voltage sweep MPPT algorithm and track to a
PWM/voltage setpoint that is either maximizing power transfer value 
(`#define __MODE__ __OPTIMIZE_POWER__`) or power efficiency ratio 
(`define __MODE__ __OPTIMIZE_EFF__`).

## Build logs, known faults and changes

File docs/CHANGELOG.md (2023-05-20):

# CHANGELOG

- [CHANGELOG](#changelog)
  - [The dark ages (Pre 3.2.0)](#the-dark-ages-pre-320)
  - [3.2.0](#320)
  - [3.3.0](#330)
  - [3.3.1](#331)
  - [3.4.0](#340)
  - [4.0.0rc (proposed)](#400rc-proposed)

---

## The dark ages (Pre 3.2.0)

- See the F2018 EE464 MPPT Final Report for list of errata and fixes.
- 0.22 uF (C21) and 10 uF (C22) capacitors in the CAN circuit schematic were
  swapped. Fixed in **v3.2.0**.

---

## 3.2.0

**Schematic**

- Reannotated all component labels and reverted rescued schematic symbols.
- Rearranged schematic and cleaned up component positioning.
- Created Array.lib for array-relevant schematic symbols.
- Swapped out zener diodes going into the uC from 3.6V to 3.9V.
- Updated the LEDs and resistors for Xx_live indicators.
- Added Error indicator LED.
- Shifted pins for voltage/current sensors to accommodate STLink UART2.
- Added fuse on the array side.
- Added unity gain filter to voltage sensors.
- Errata: swapped 0.22uF and 10uF capacitors on CAN circuit to correct positions.

**Layout**

- Created MPPT-PrimaryPCB.pretty for custom footprints.
- Specified that board should be 2oz copper/ft.
- Re-specified snubber circuit footprints.
- Comprehensive redesign of layout.

---

## 3.3.0

**Schematic**

- BoM consolidation to JLCPCB.
- BoM merged into schematic component fields.
- Removed RC filters from voltage sensors.
- Replaced MAX chip with LM358.
- Downshifted 3.9V zeners to 3.3V.
- Removed general purpose switching diodes.

**Layout**

- Moved footprints from MPPT-PrimaryPCB.pretty to Footprints.
- Dropped copper weight down to 1oz/ft.
- Places JLCPCB passives on same side.
- Reduced power path area.
- Moved sensor paths away from high power current path.
- Stitching vias and secondary GND plane for thermal and EMI improvement.

---

## 3.3.1

**Schematic**

- Vout and GNDout pins swapped to correct pins for IES01_PDS1 (U4).
- EN pin for UCC37321 given an MCU DIO to be SW ambiguous to UCC37321, UCC37322 (U3).
- Maxim Integrated 40075 voltage op amp switched to TI OPA990 to run on +9VA.

**Layout**

- Slight changes around power, gate driver routing.

---

## 3.4.0

- Versioning is unified between schematic, layout, and BoM.
- This repo is now a subrepo in the Power-Generation monorepo.

**Schematic**

- Schematic has been broken into hierarchical sheets and all components are
  re-enumerated for future extensibility.
- Snubber values are finalized.

**Layout**

- Layout silkscreen is updated.

## 4.0.0rc (proposed)

- Proposal to use modified design from
  [MPPT-design](https://github.com/dimembermatt/MPPT-Design), particularly
  v0.2.0.

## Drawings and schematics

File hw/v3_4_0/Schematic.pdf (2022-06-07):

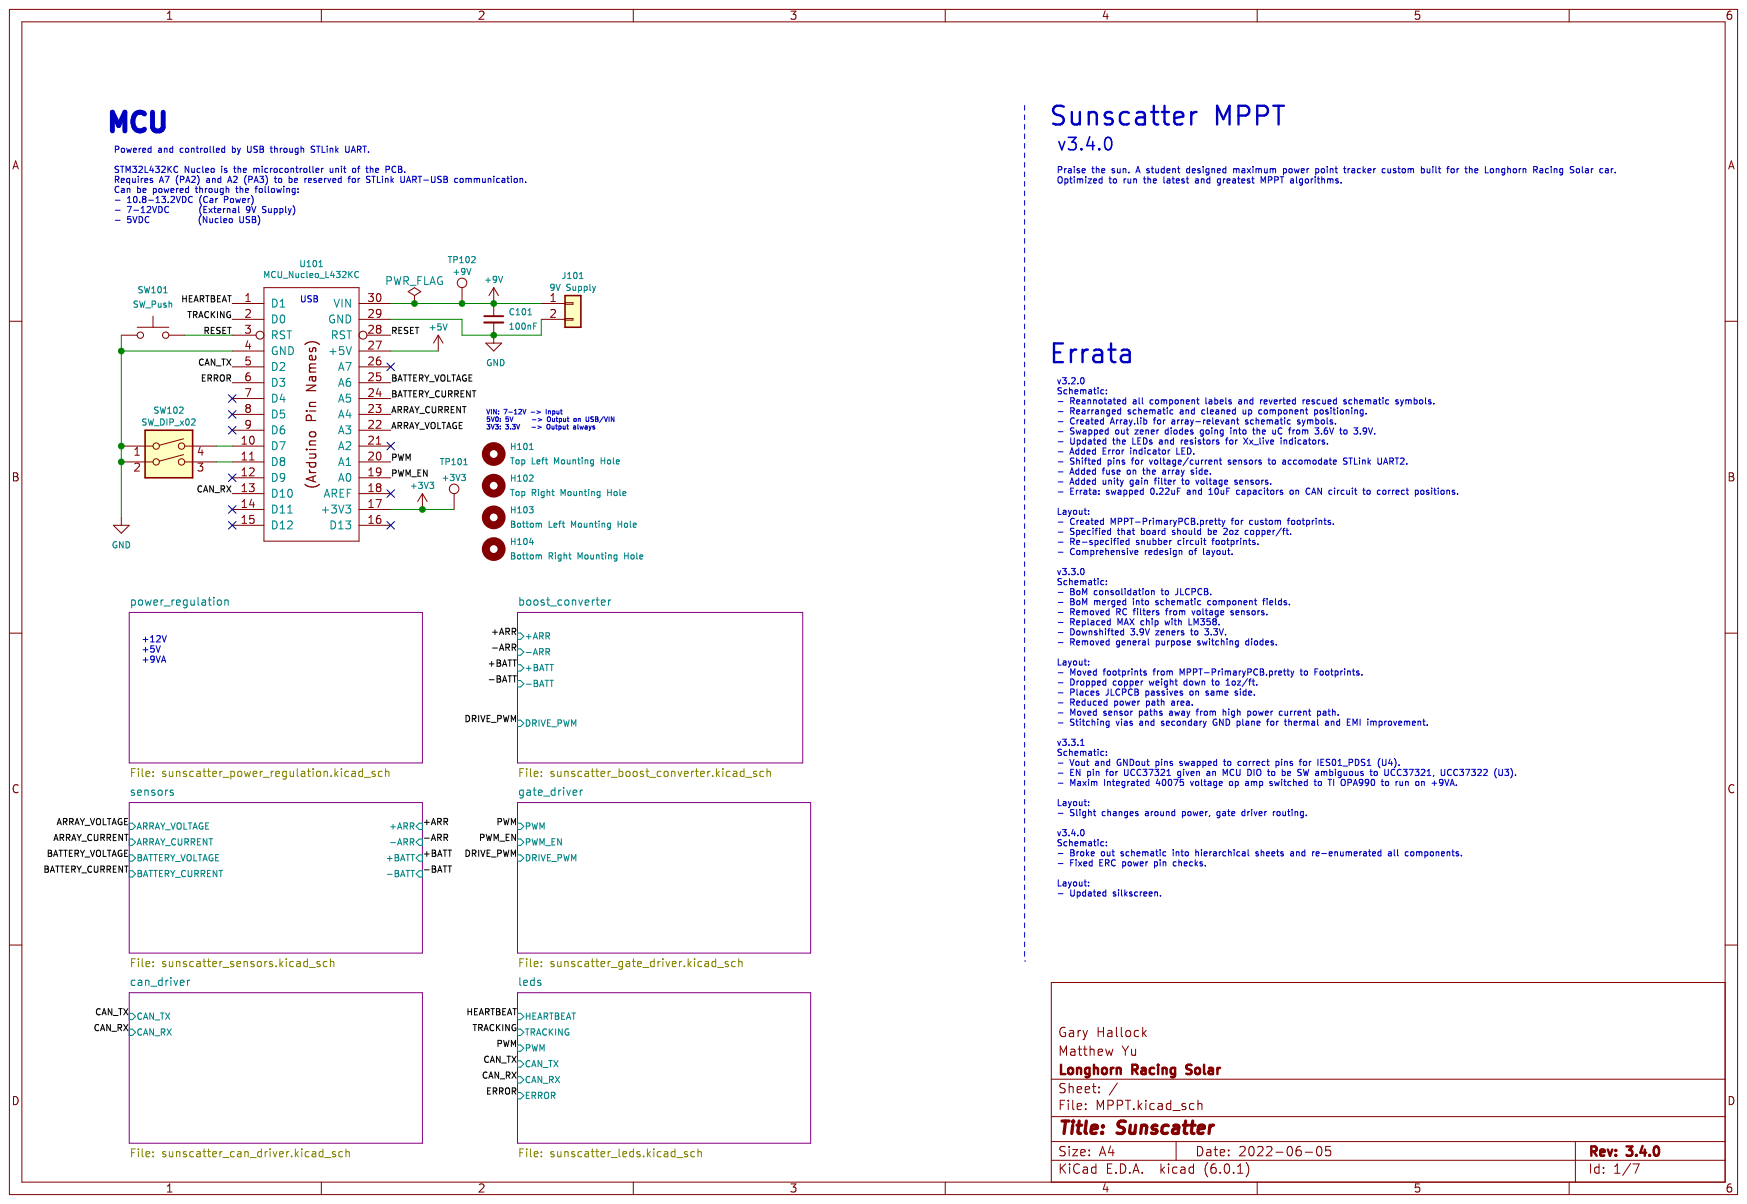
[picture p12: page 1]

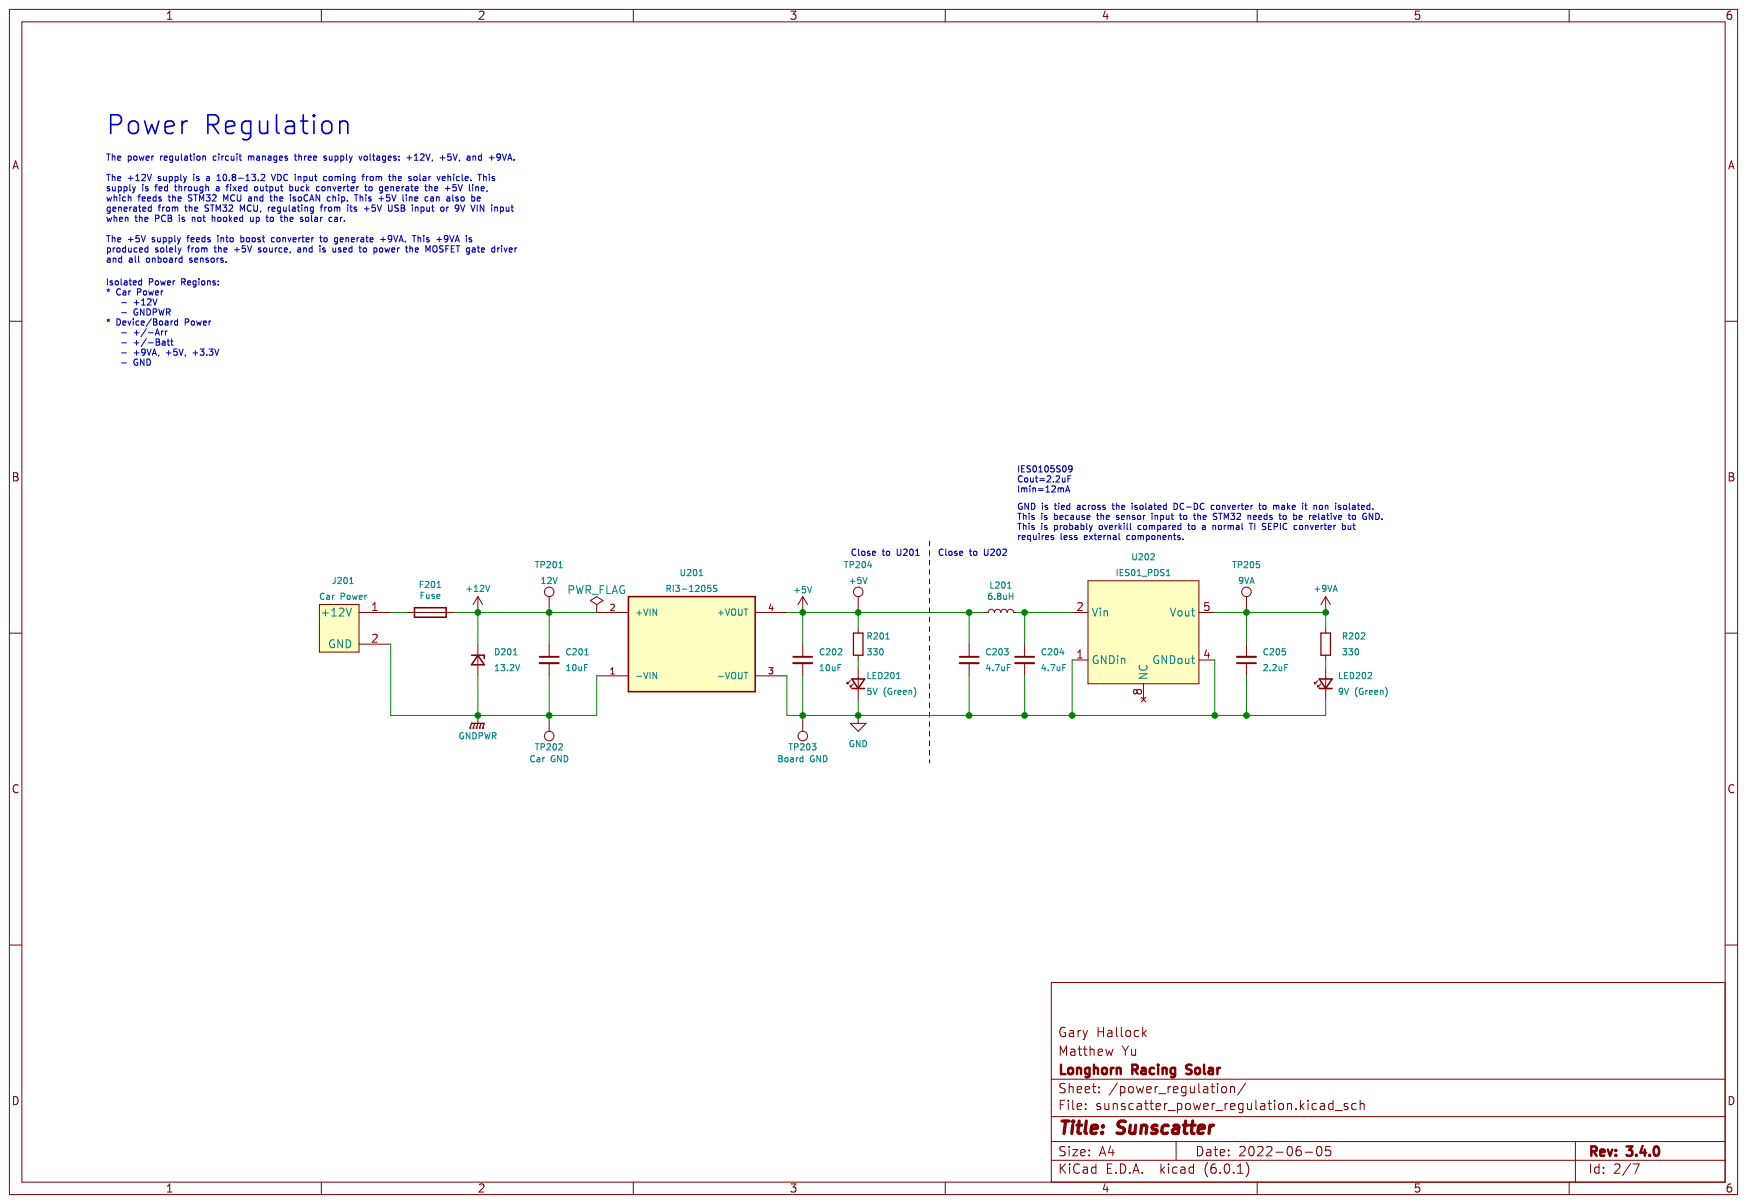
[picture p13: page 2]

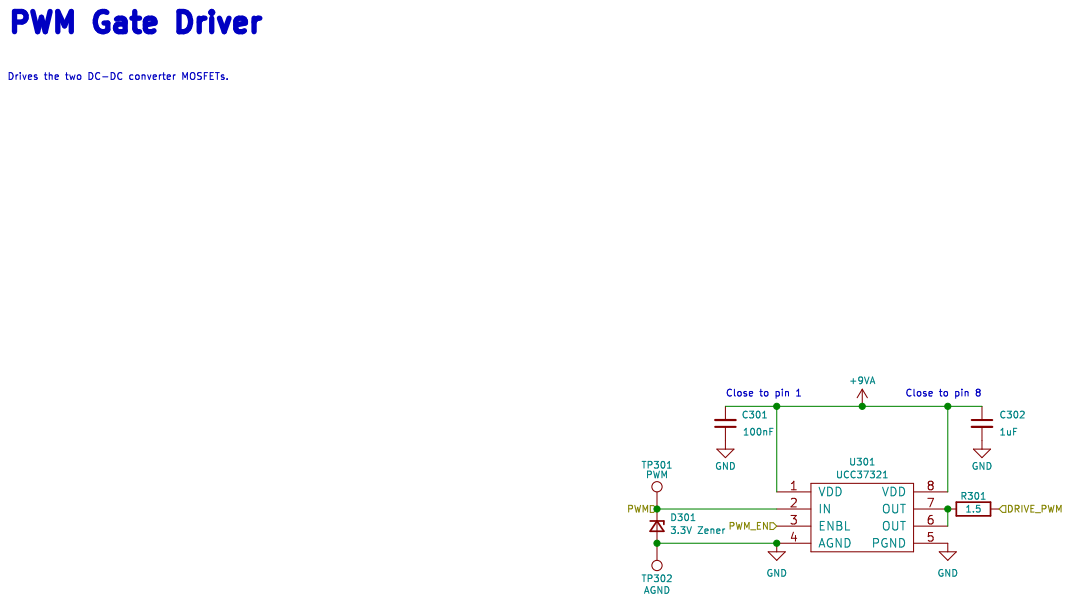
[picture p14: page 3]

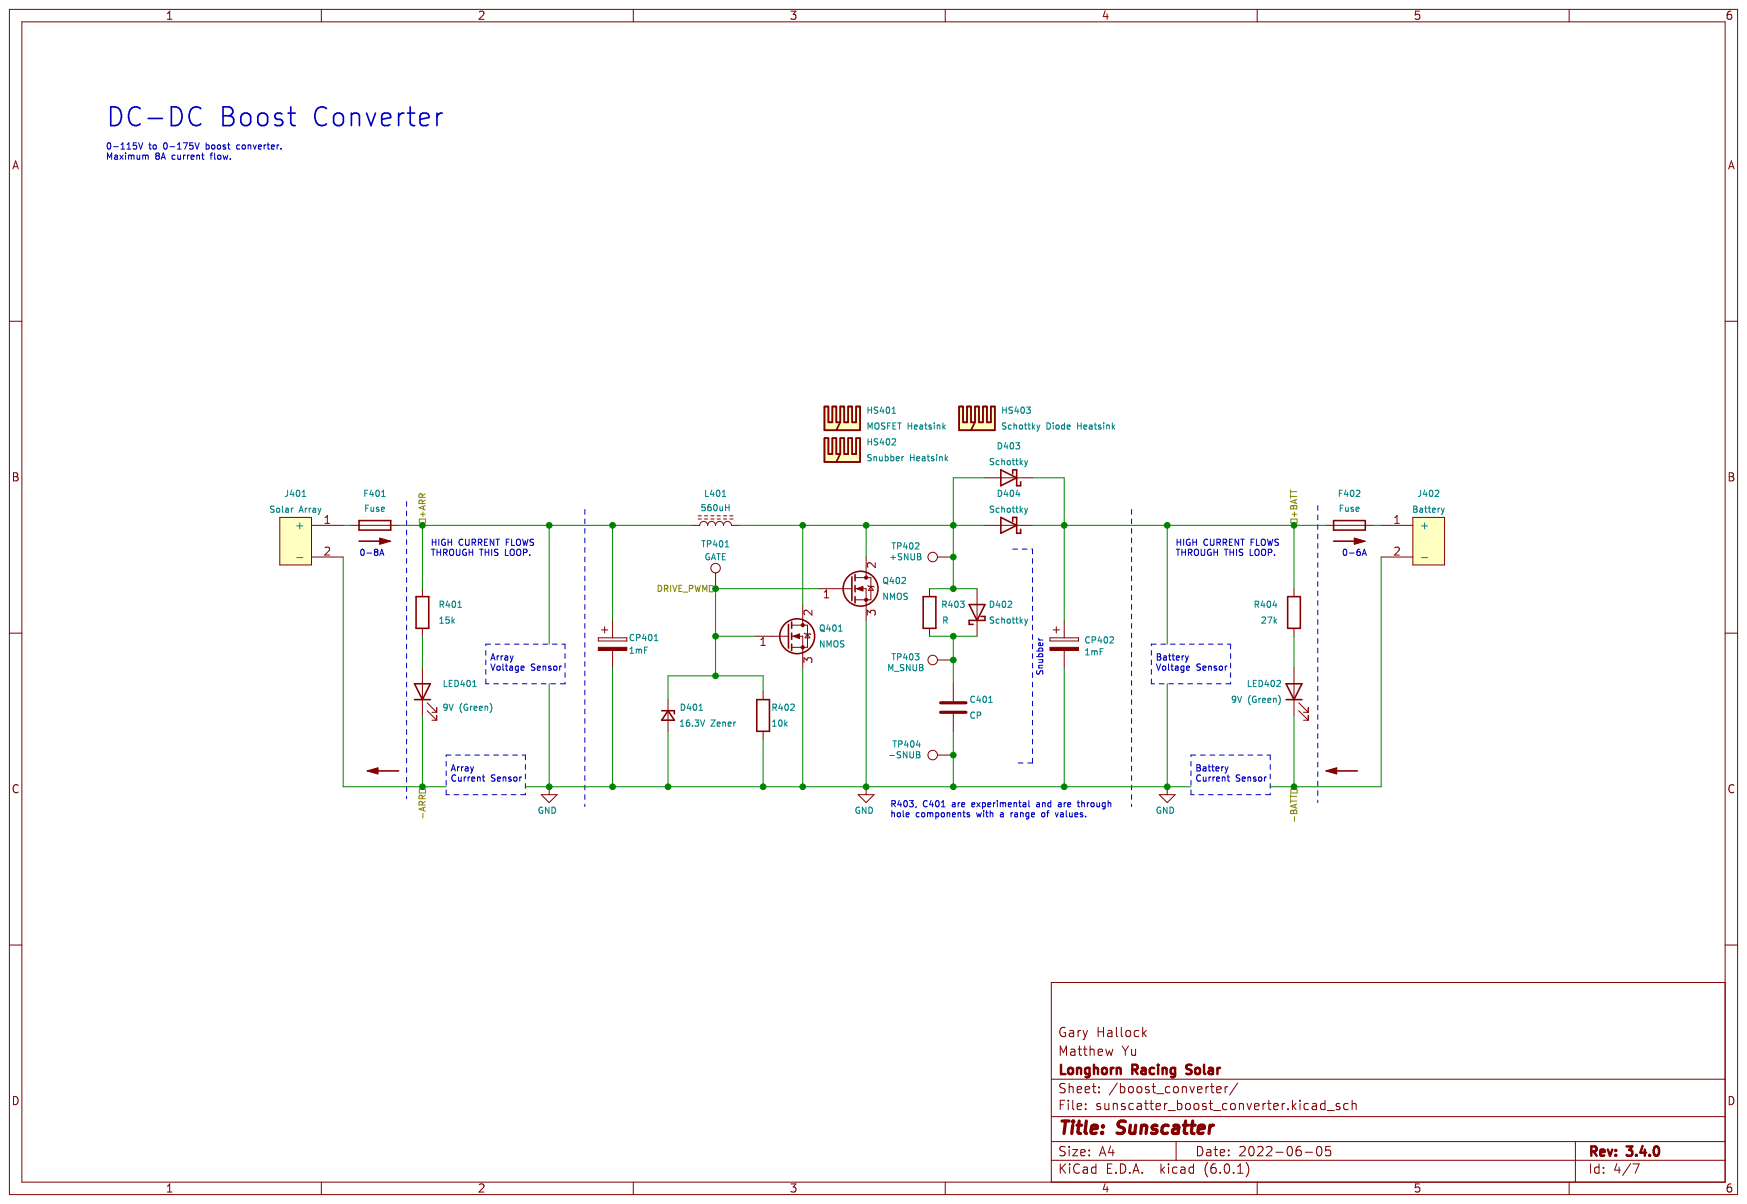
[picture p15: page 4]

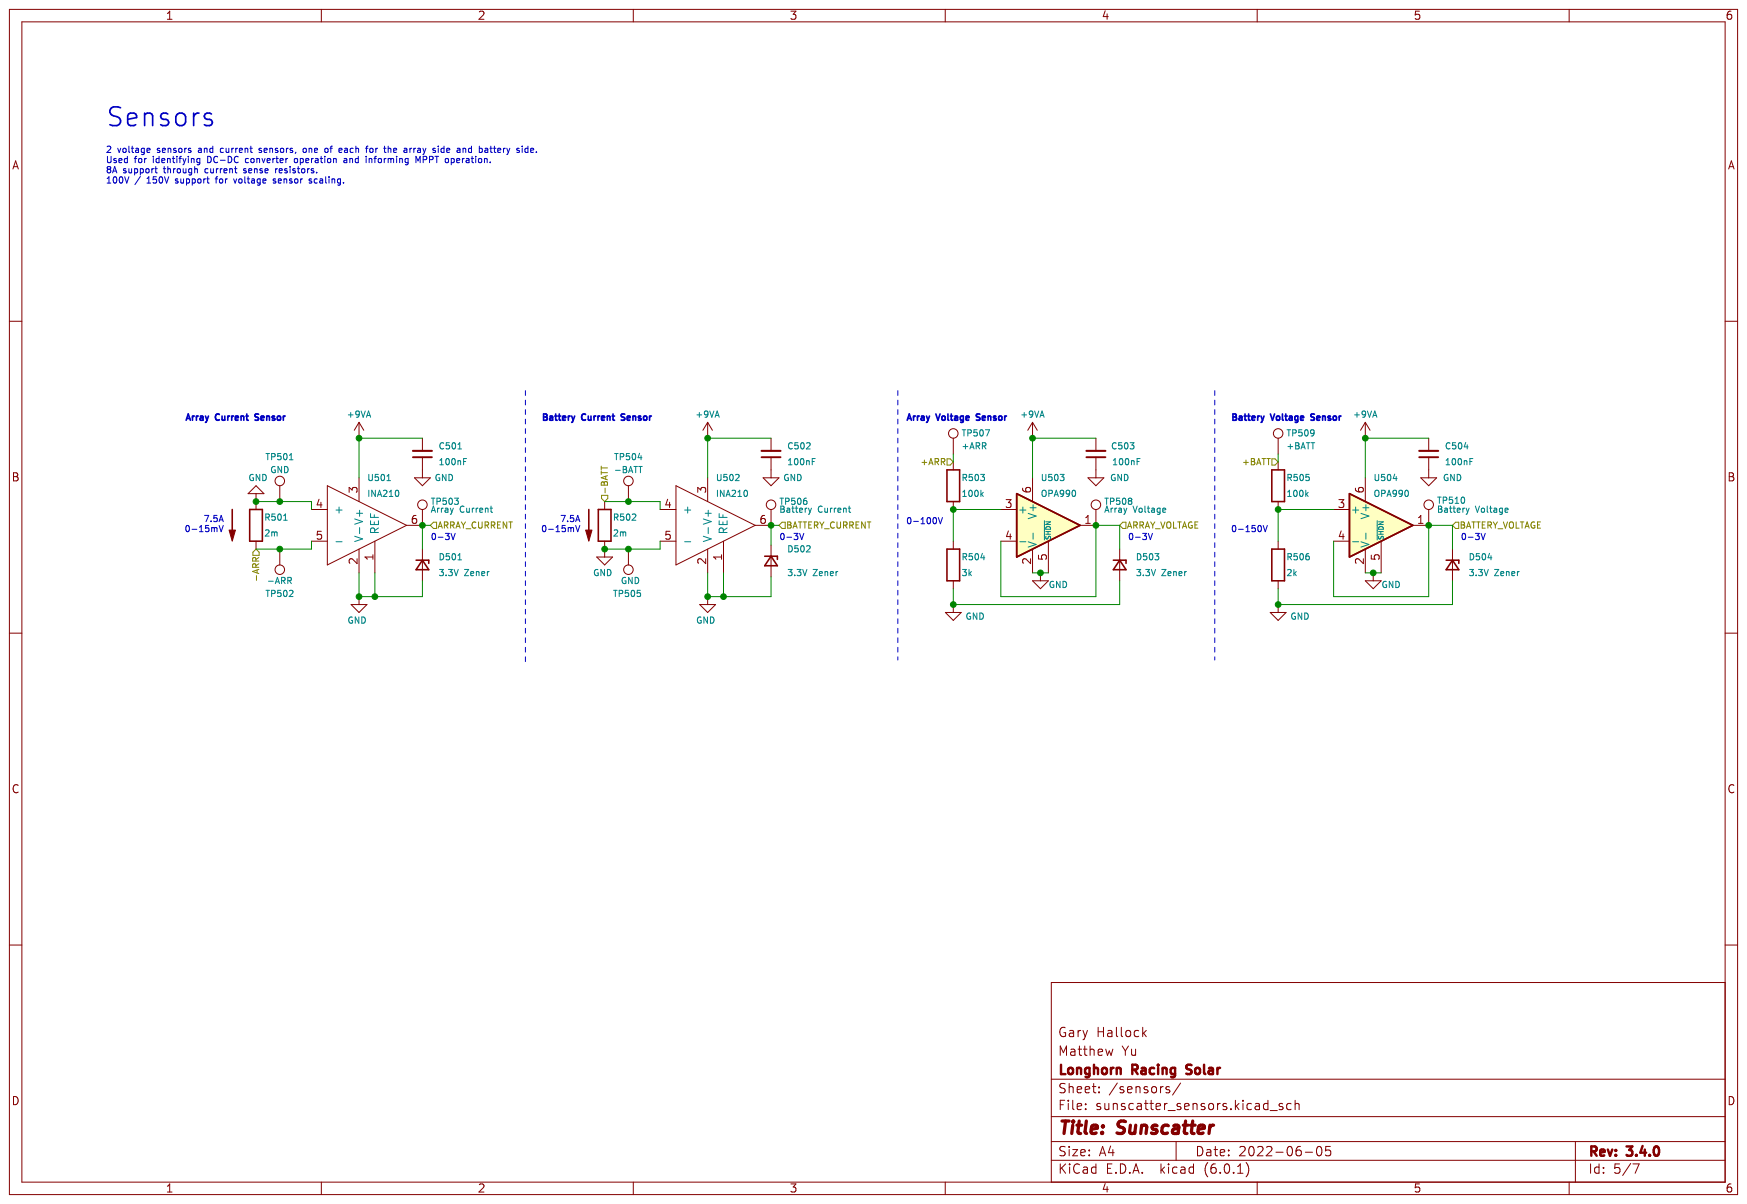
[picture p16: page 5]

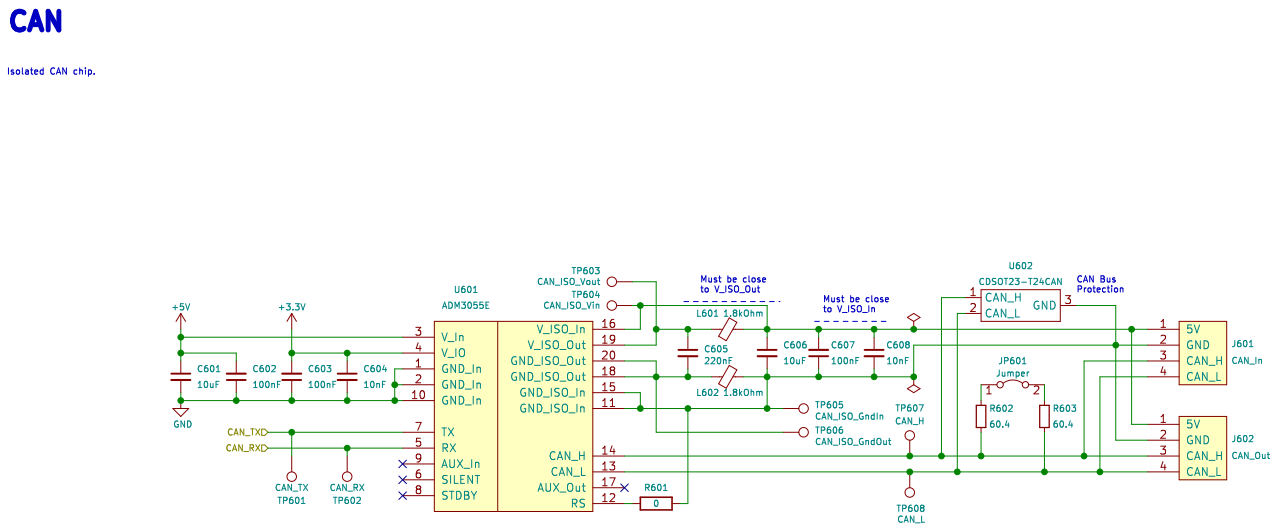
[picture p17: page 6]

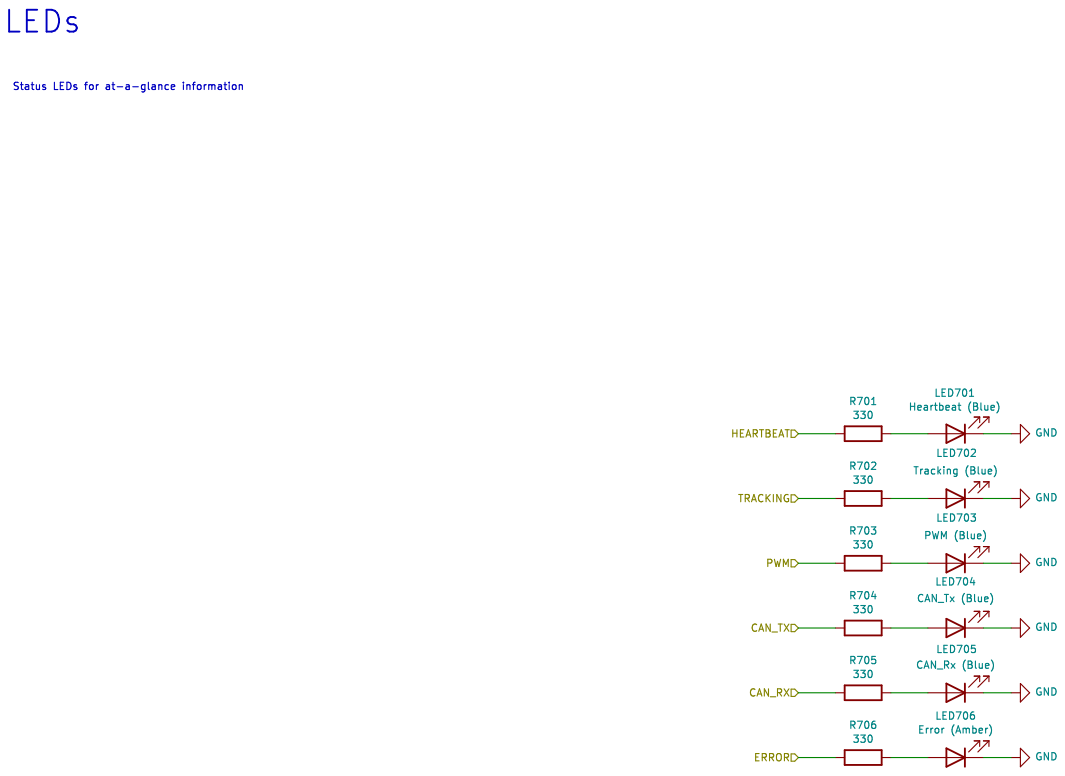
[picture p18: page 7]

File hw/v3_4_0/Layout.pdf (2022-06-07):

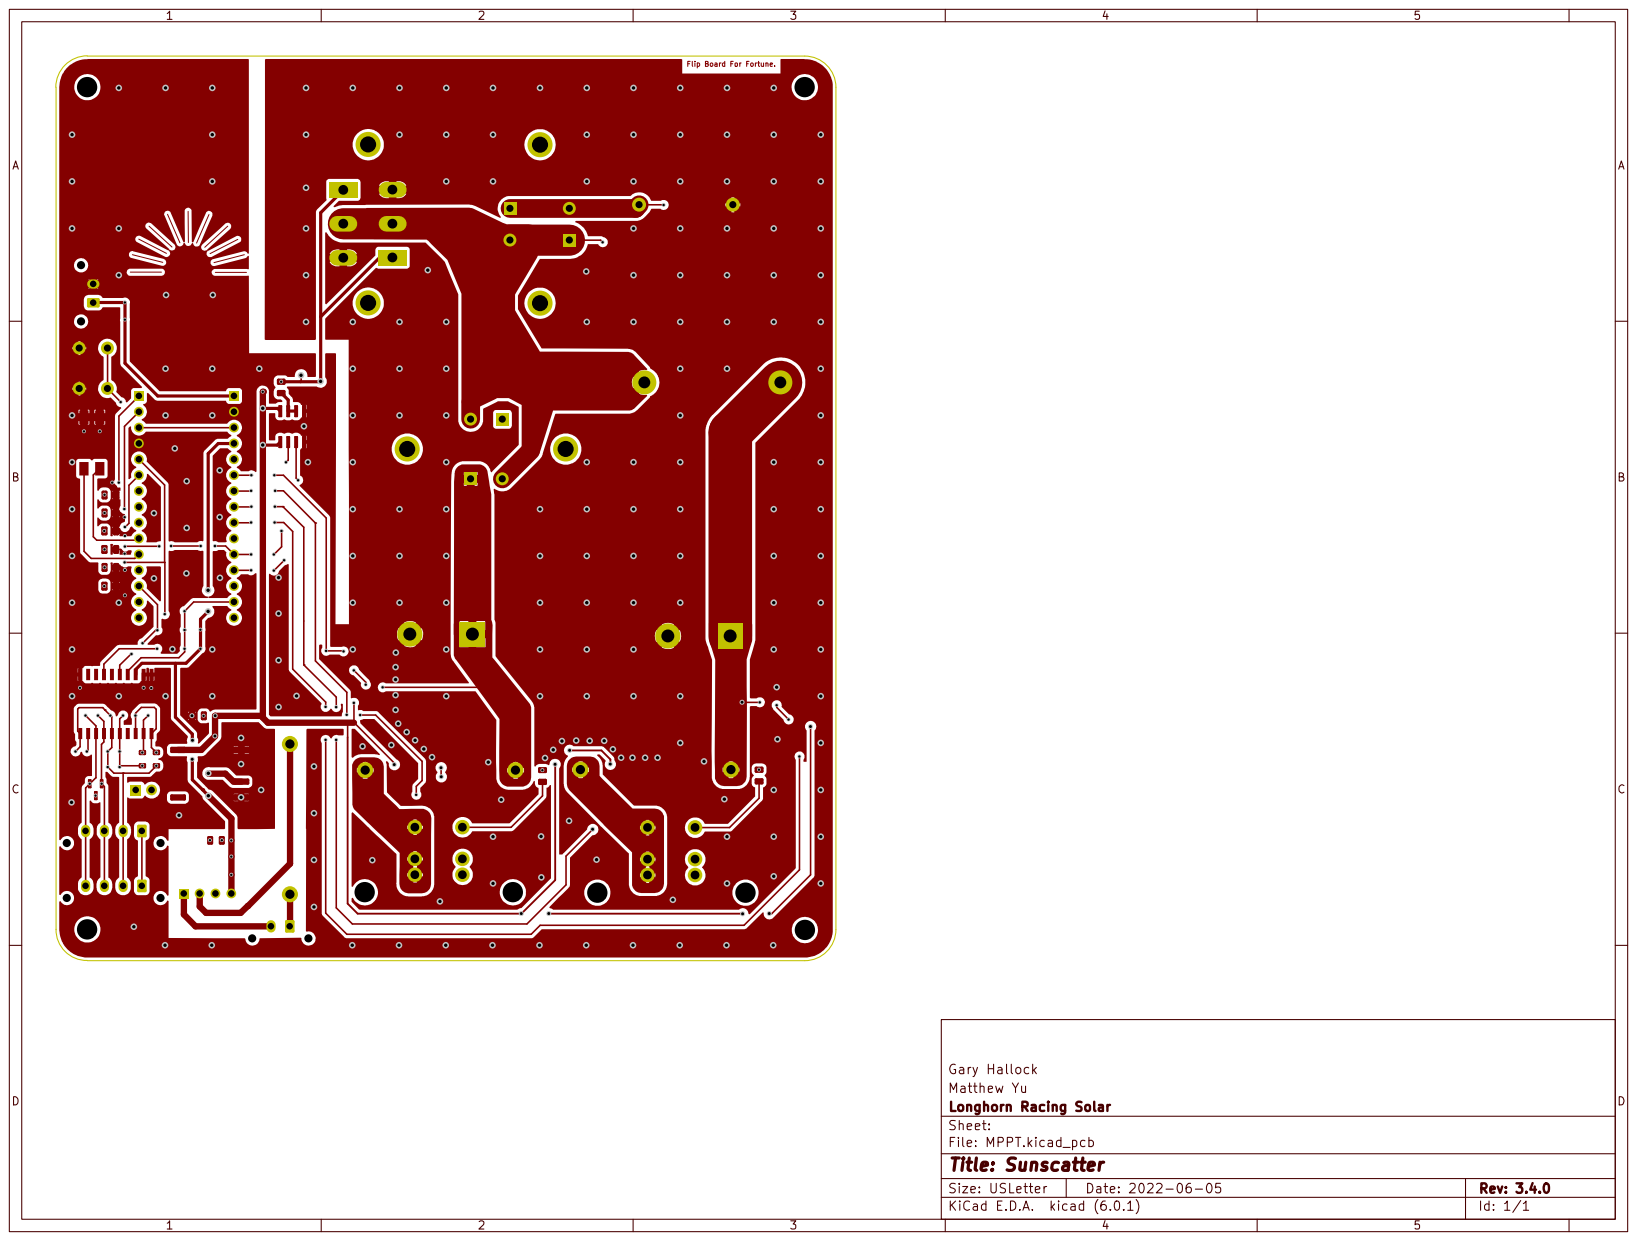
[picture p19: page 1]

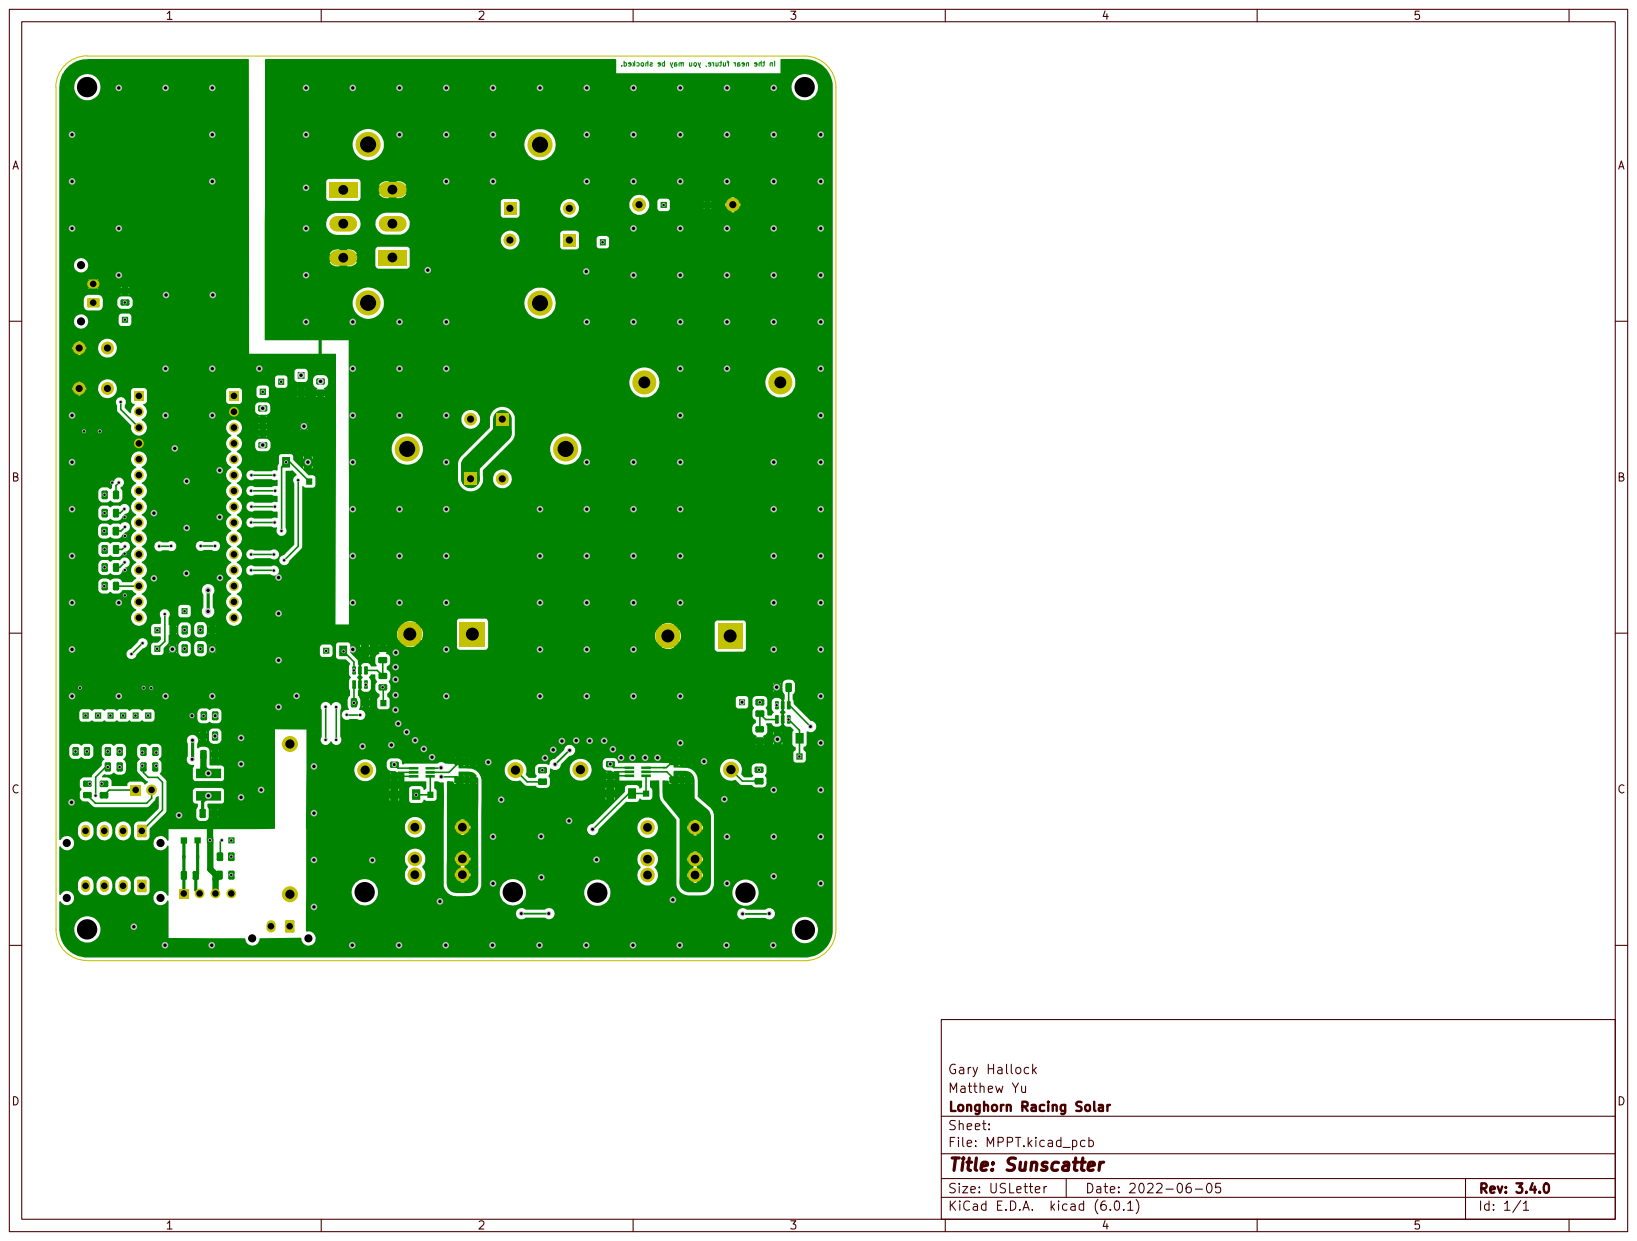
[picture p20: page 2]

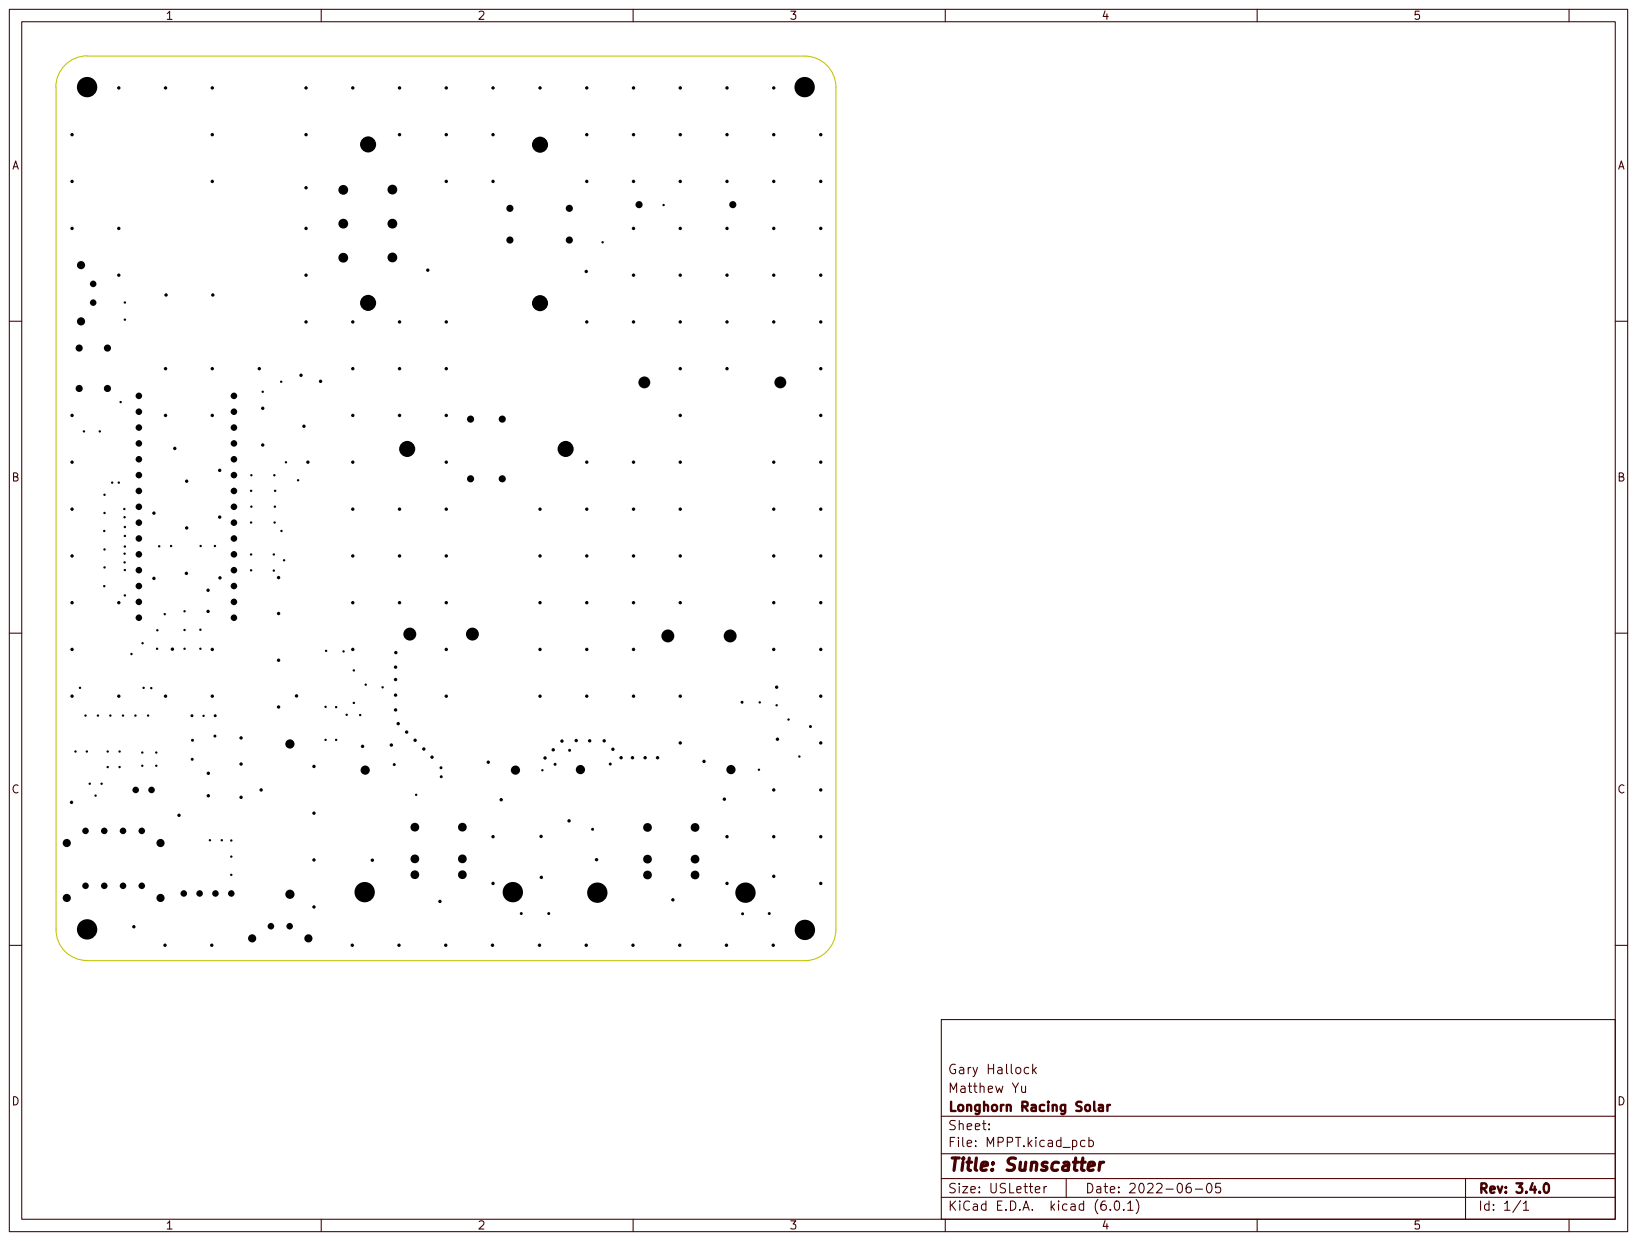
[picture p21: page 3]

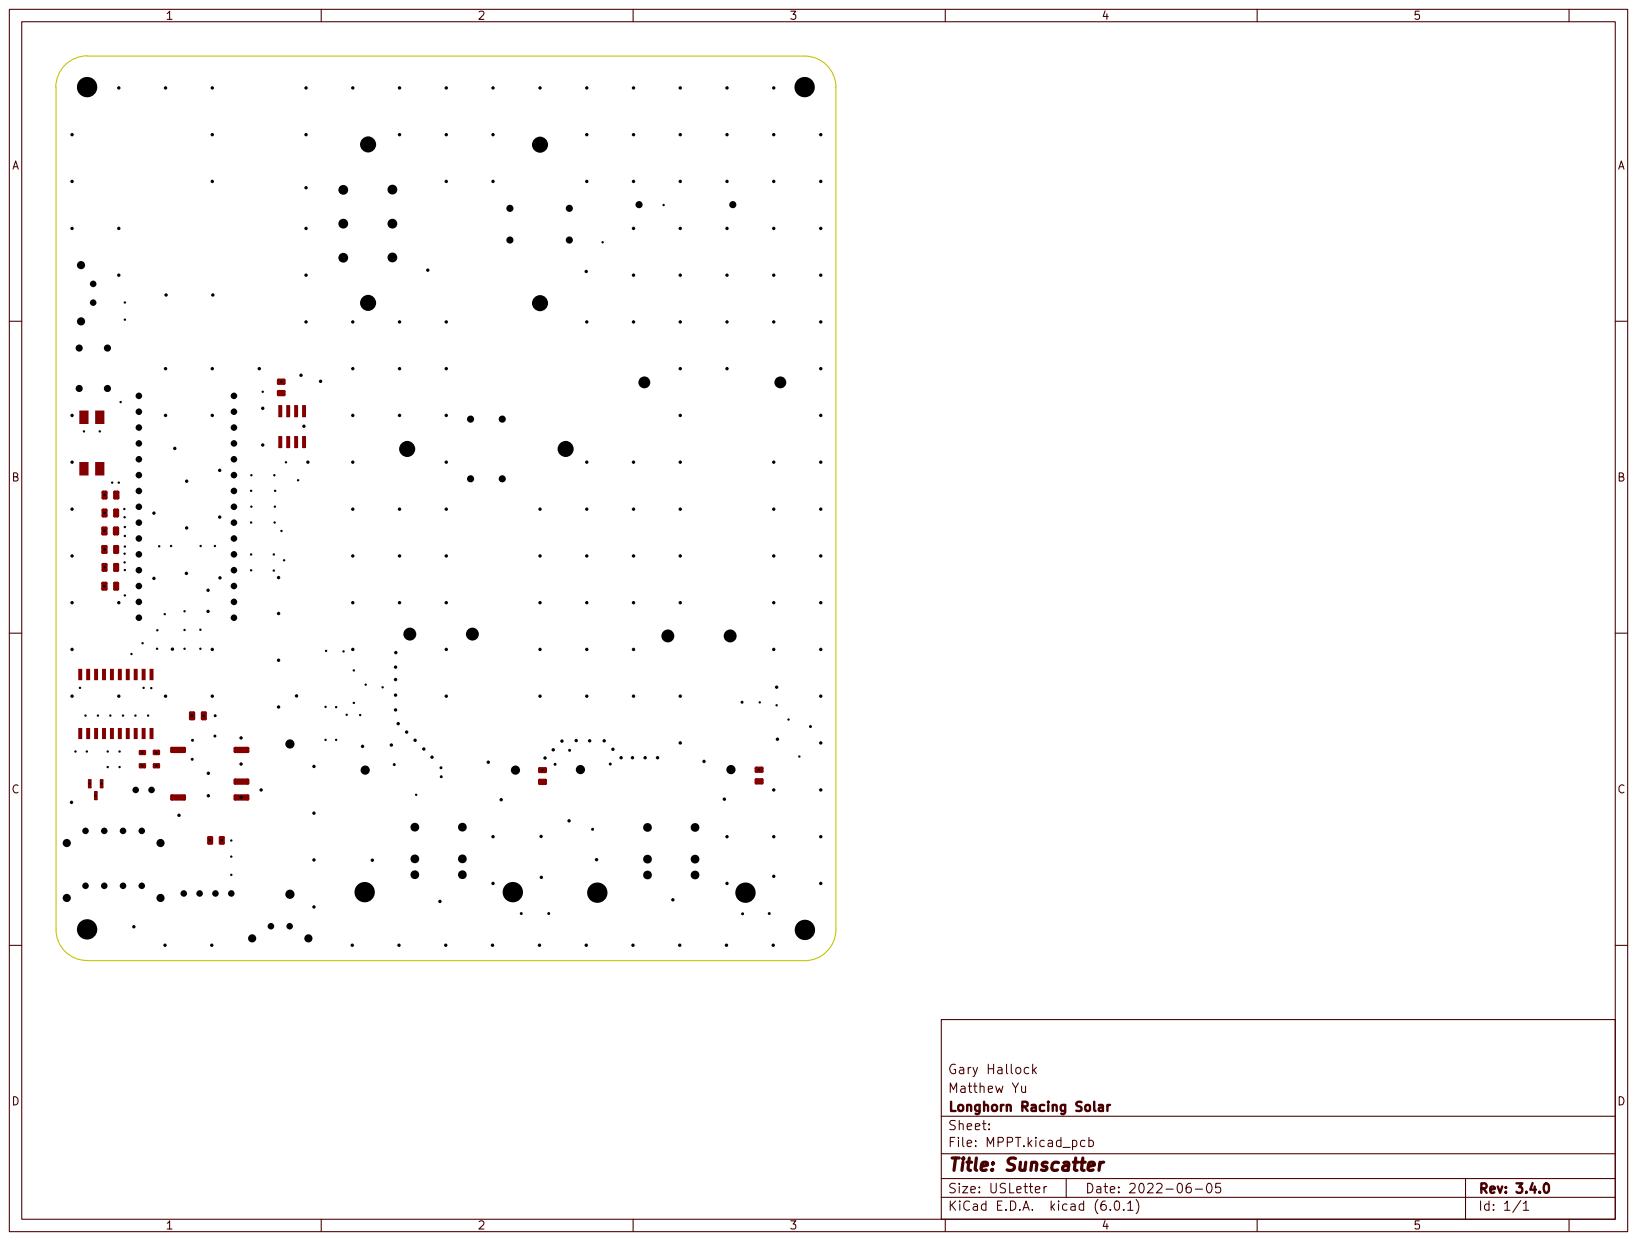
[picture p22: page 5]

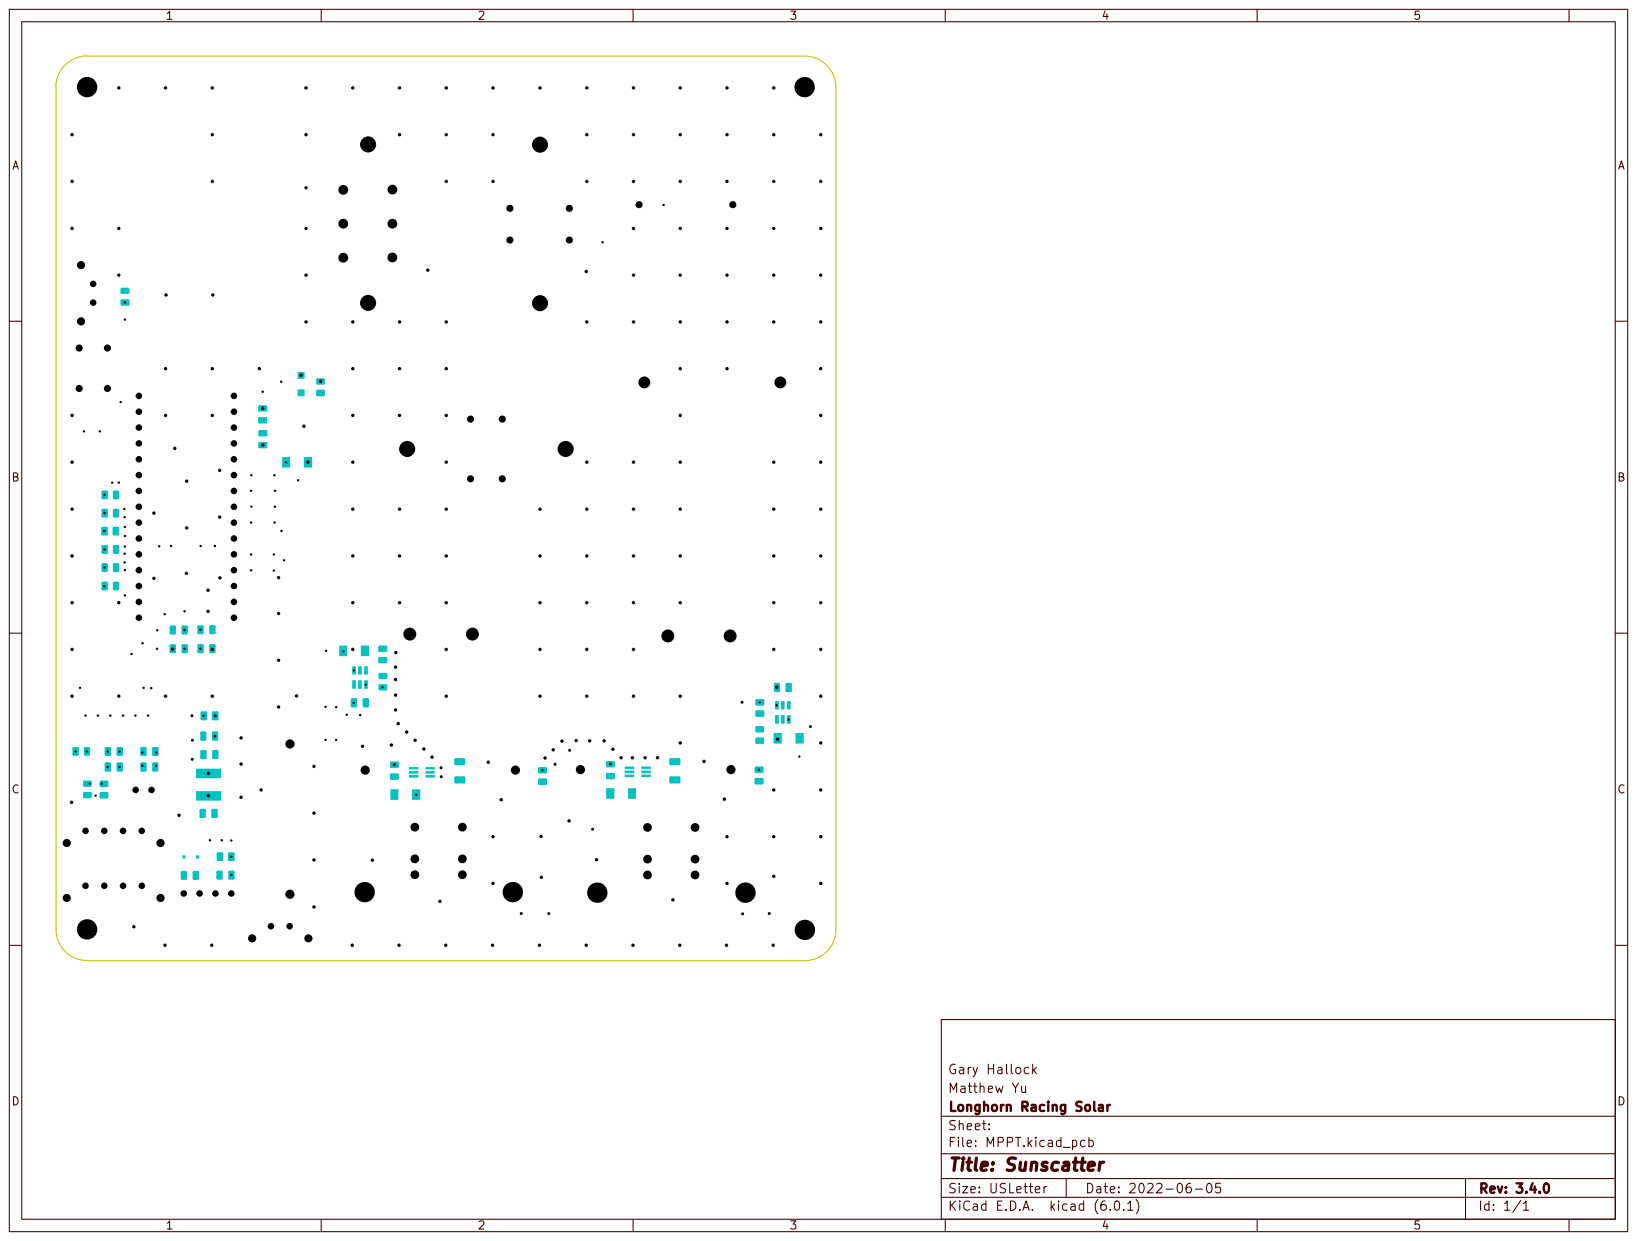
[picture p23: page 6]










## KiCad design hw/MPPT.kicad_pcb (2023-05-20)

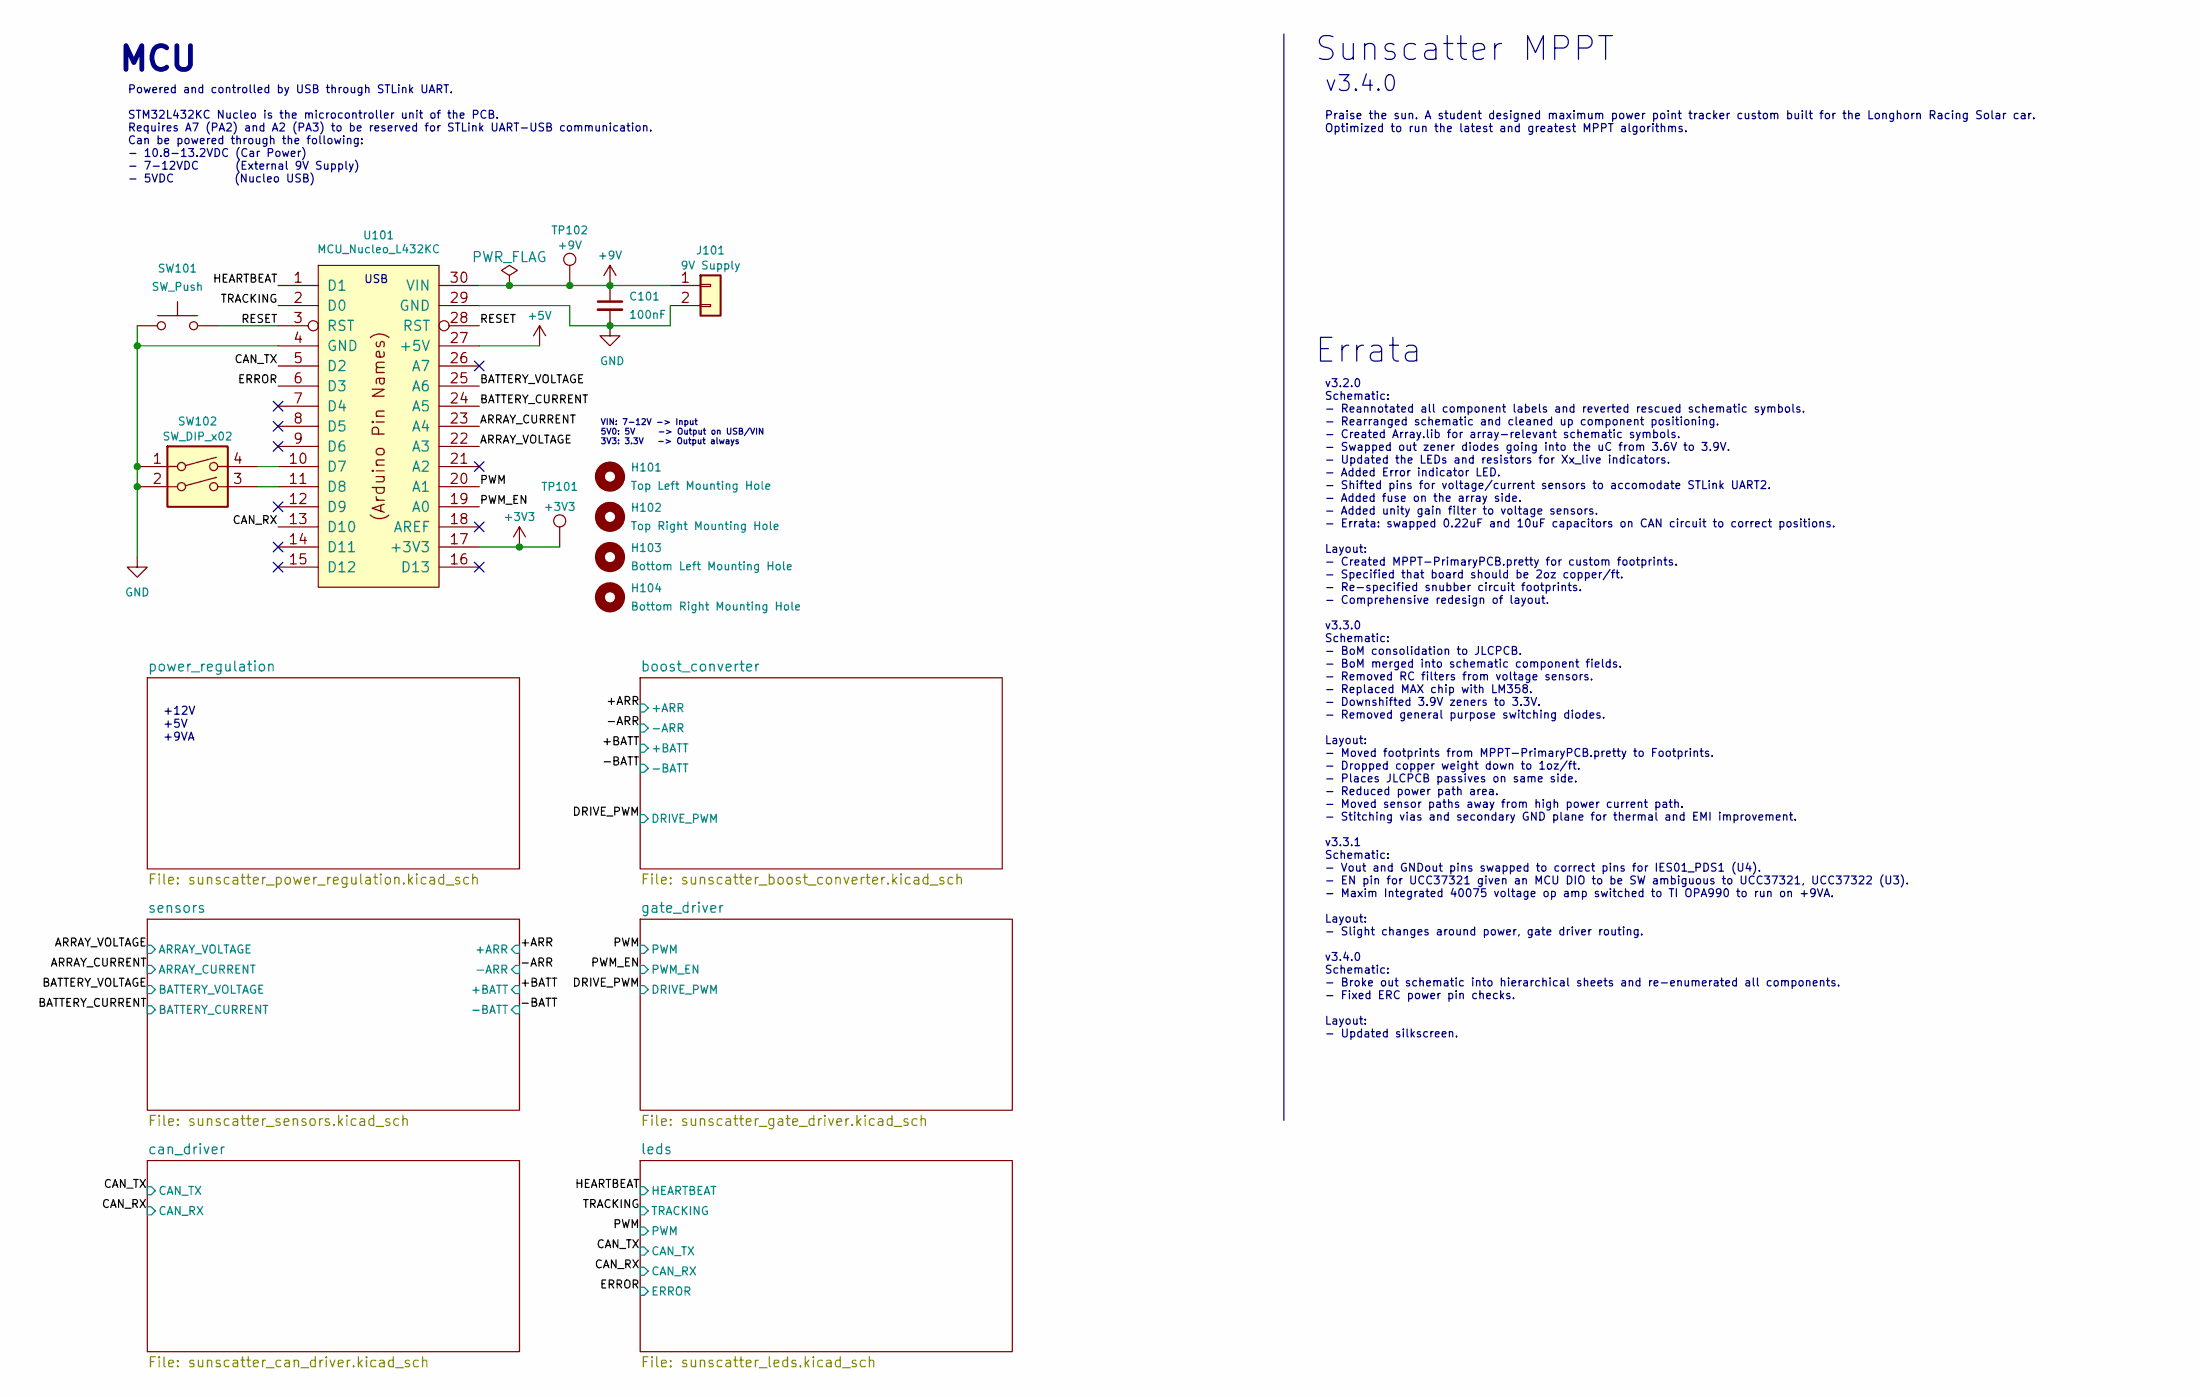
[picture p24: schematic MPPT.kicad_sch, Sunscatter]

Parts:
C101: 100nF; C_0805_2012Metric; Manufacturer Part Number CL21B104KCFNNNE; JLCPCB BOM 1
H101: Top Left Mounting Hole; MountingHole_3.2mm_M3
H102: Top Right Mounting Hole; MountingHole_3.2mm_M3
H103: Bottom Left Mounting Hole; MountingHole_3.2mm_M3
H104: Bottom Right Mounting Hole; MountingHole_3.2mm_M3
J101: 9V Supply; Molex_Micro-Fit_3.0_43650-0215_1x02_P3.00mm_Vertical; Manufacturer Part Number 43650-0215; JLCPCB BOM 0
SW101: SW_Push; SW_PUSH_6mm; Manufacturer Part Number TS02-66-50-BK-260-SCR-D; JLCPCB BOM 0
SW102: SW_DIP_x02; ADF02ST04_DIP_Switch_2_POS; Manufacturer Part Number ADF02ST04; JLCPCB BOM 0
TP101: +3V3; TestPoint_Pad_1.0x1.0mm
TP102: +9V; TestPoint_Pad_1.0x1.0mm
U101: MCU_Nucleo_L432KC; MODULE_NUCLEO-L432KC; Manufacturer Part Number 511-NUCLEO-L432KC; JLCPCB BOM 0

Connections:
+5V: U101.27 (+5V); also elsewhere on the board
+9V: C101.1, J101.1, TP102.1, U101.30 (VIN)
/ARRAY_CURRENT: U101.23 (A4); also elsewhere on the board
/ARRAY_VOLTAGE: U101.22 (A3); also elsewhere on the board
/BATTERY_CURRENT: U101.24 (A5); also elsewhere on the board
/BATTERY_VOLTAGE: U101.25 (A6); also elsewhere on the board
/CAN_RX: U101.13 (D10); also elsewhere on the board
/CAN_TX: U101.5 (D2); also elsewhere on the board
/ERROR: U101.6 (D3); also elsewhere on the board
/HEARTBEAT: U101.1 (D1); also elsewhere on the board
/PWM: U101.20 (A1); also elsewhere on the board
/PWM_EN: U101.19 (A0); also elsewhere on the board
/RESET: SW101.2, U101.3 (RST), U101.28 (RST)
/TRACKING: U101.2 (D0); also elsewhere on the board
GND: C101.2, J101.2, SW101.1, SW102.1, SW102.2, U101.4 (GND), U101.29 (GND); also elsewhere on the board
unnamed: SW102.3, U101.11 (D8)
unnamed: SW102.4, U101.10 (D7)

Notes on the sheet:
Errata
VIN: 7-12V -> Input 5V0: 5V -> Output on USB/VIN 3V3: 3.3V -> Output always
USB
v3.2.0 Schematic: - Reannotated all component labels and reverted rescued schematic symbols. - Rearranged schematic and cleaned up component positioning. - Created Array.lib for array-relevant schematic symbols. - Swapped out zener diodes going into the uC from 3.6V to 3.9V. - Updated the LEDs and 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
v3.4.0
Powered and controlled by USB through STLink UART. STM32L432KC Nucleo is the microcontroller unit of the PCB. Requires A7 (PA2) and A2 (PA3) to be reserved for STLink UART-USB communication. Can be powered through the following: - 10.8-13.2VDC (Car Power) - 7-12VDC (External 9V Supply) - 5VDC (Nucl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
MCU
Sunscatter MPPT
+12V +5V +9VA
Praise the sun. A student designed maximum power point tracker custom built for the Longhorn Racing Solar car. Optimized to run the latest and greatest MPPT algorithms.

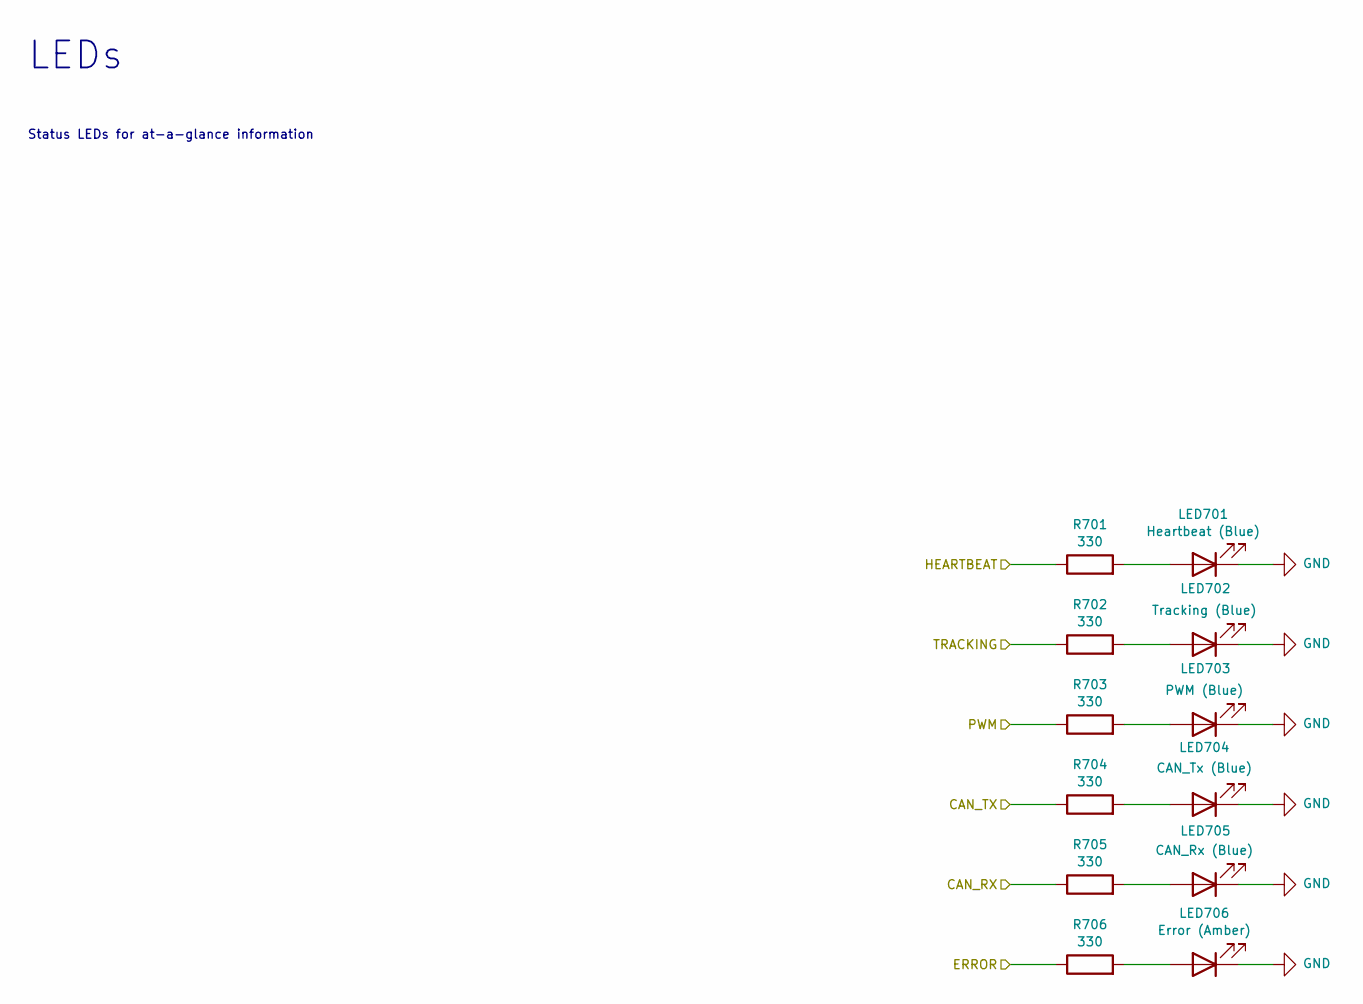
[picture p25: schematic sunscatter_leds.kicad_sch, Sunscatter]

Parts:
LED701: Heartbeat (Blue); LED_0805_2012Metric; Manufacturer Part Number APTD2012LQBC/D; JLCPCB BOM 0
LED702: Tracking (Blue); LED_0805_2012Metric; Manufacturer Part Number APTD2012LQBC/D; JLCPCB BOM 0
LED703: PWM (Blue); LED_0805_2012Metric; Manufacturer Part Number APTD2012LQBC/D; JLCPCB BOM 0
LED704: CAN_Tx (Blue); LED_0805_2012Metric; Manufacturer Part Number APTD2012LQBC/D; JLCPCB BOM 0
LED705: CAN_Rx (Blue); LED_0805_2012Metric; Manufacturer Part Number APTD2012LQBC/D; JLCPCB BOM 0
LED706: Error (Amber); LED_0805_2012Metric; Manufacturer Part Number APTD2012LSURCK; JLCPCB BOM 0
R701, R702, R703, R704, R705, R706: 330; R_0805_2012Metric; Manufacturer Part Number 0805W8F3300T5E; JLCPCB BOM 1

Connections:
/CAN_RX: R705.1; also elsewhere on the board
/CAN_TX: R704.1; also elsewhere on the board
/ERROR: R706.1; also elsewhere on the board
/HEARTBEAT: R701.1; also elsewhere on the board
/PWM: R703.1; also elsewhere on the board
/TRACKING: R702.1; also elsewhere on the board
GND: LED701.1 (K), LED702.1 (K), LED703.1 (K), LED704.1 (K), LED705.1 (K), LED706.1 (K); also elsewhere on the board
unnamed: LED701.2 (A), R701.2
unnamed: LED702.2 (A), R702.2
unnamed: LED703.2 (A), R703.2
unnamed: LED704.2 (A), R704.2
unnamed: LED705.2 (A), R705.2
unnamed: LED706.2 (A), R706.2

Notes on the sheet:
Status LEDs for at-a-glance information
LEDs

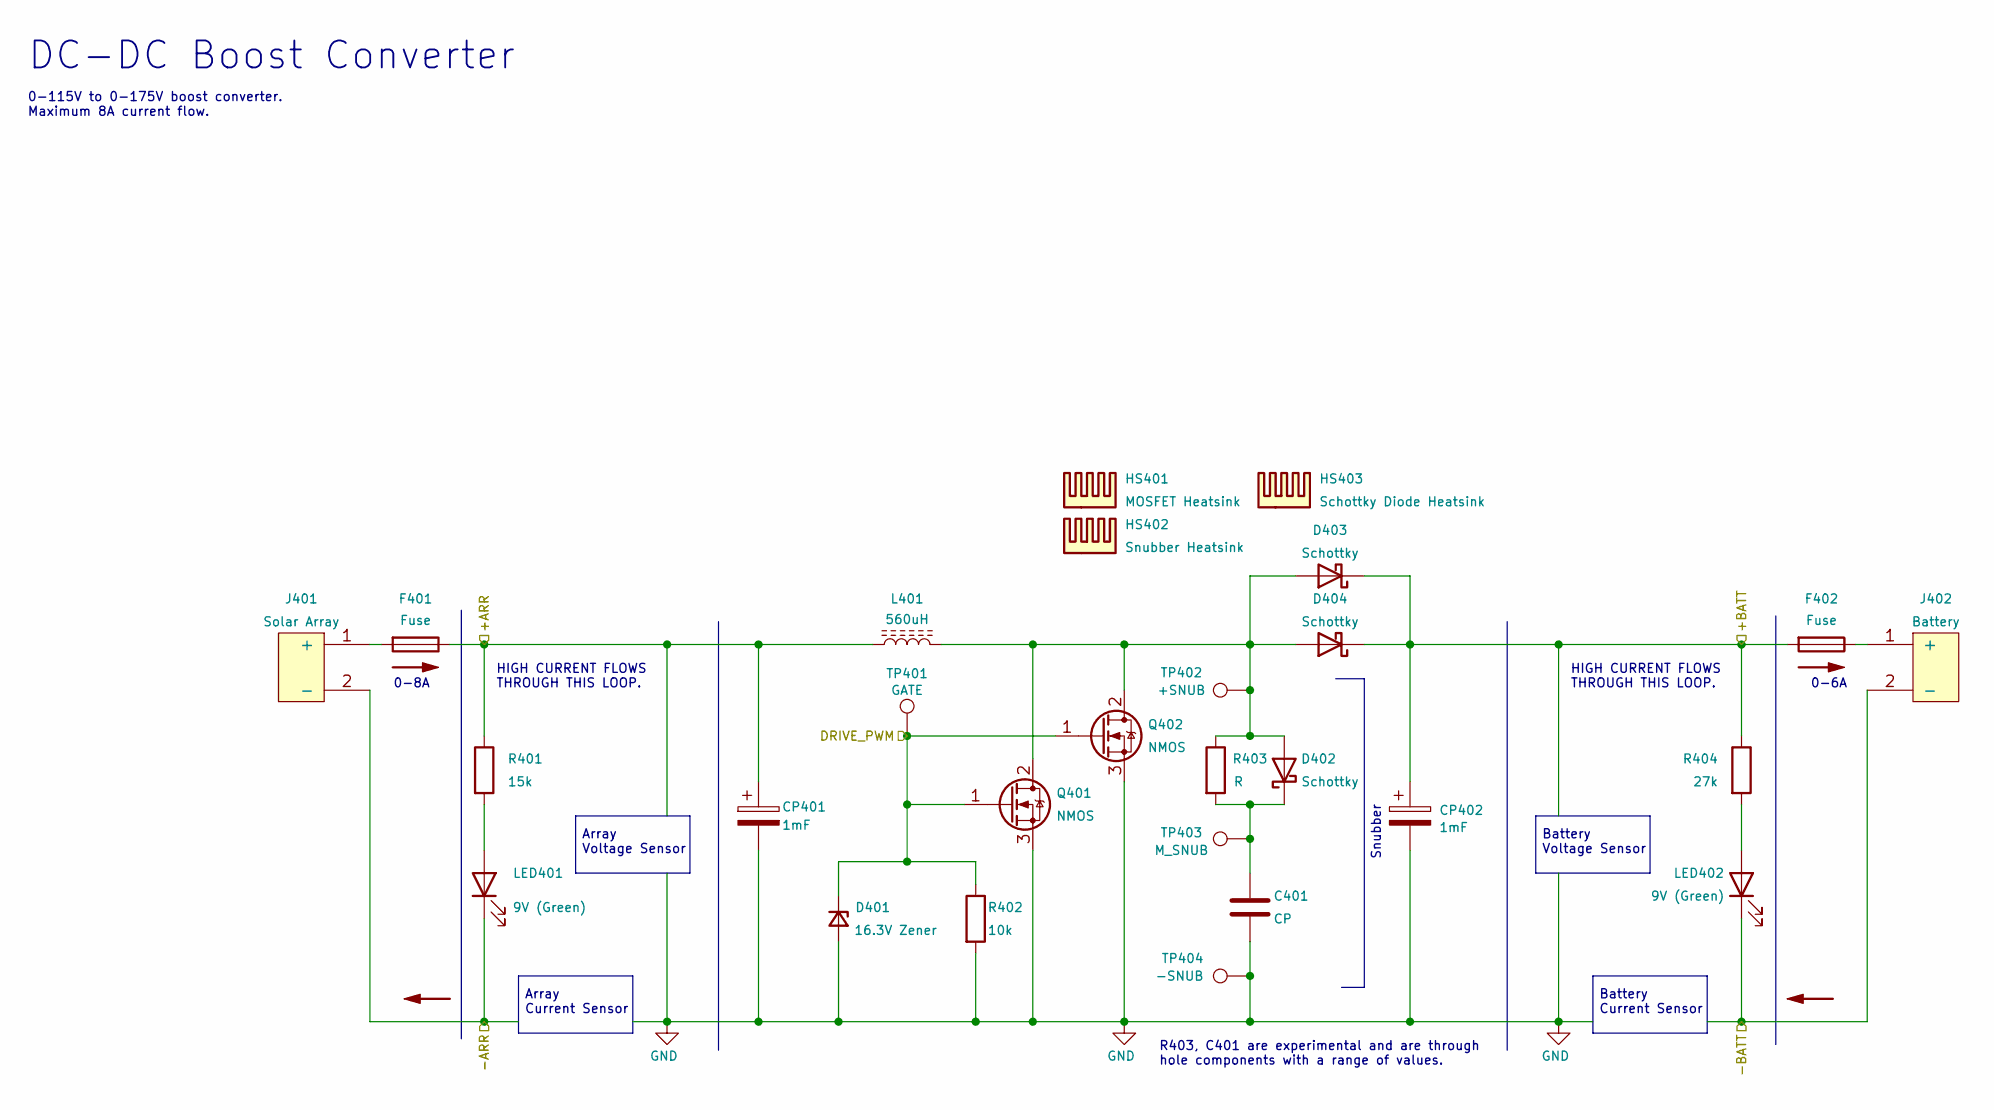
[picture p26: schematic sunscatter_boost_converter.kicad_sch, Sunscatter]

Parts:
C401: CP; C_Rect_L16.5mm_W7.0mm_P15.00mm_MKT; Mouser Part 75-MKT1813247635; JLCPCB BOM 0
CP401, CP402: 1mF; CP_Radial_D30.0mm_P10.00mm_SnapIn; Manufacturer Part Number SLPX102M250E5P3; JLCPCB BOM 0
D401: 16.3V Zener; D_SOD-123F; Manufacturer Part Number BZT52H-B16,115; JLCPCB BOM 0
D402, D403, D404: Schottky; TO-220-2_Vertical; Manufacturer Part Number SCS308AHGC9; JLCPCB BOM 0
F401, F402: Fuse; 05200101Z_Fuze_Holder_5x20_PCB_Mount; Manufacturer Part Number 05200101Z; JLCPCB BOM 0
HS401: MOSFET Heatsink; Heatsink_Fischer_SK129-STS_42x25mm_2xDrill2.5mm; Manufacturer Part Number FA-T220-38E; JLCPCB BOM 0
HS402: Snubber Heatsink; Heatsink_Fischer_SK129-STS_42x25mm_2xDrill2.5mm; Manufacturer Part Number FA-T220-38E; JLCPCB BOM 0
HS403: Schottky Diode Heatsink; Heatsink_Fischer_SK129-STS_42x25mm_2xDrill2.5mm; Manufacturer Part Number FA-T220-38E; JLCPCB BOM 0
J401: Solar Array; PhoenixContact_PowerCombicon5_GF_2x7.62mm; Manufacturer Part Number 1720796; JLCPCB BOM 0
J402: Battery; PhoenixContact_PowerCombicon5_GF_2x7.62mm; Manufacturer Part Number 1720796; JLCPCB BOM 0
L401: 560uH; L_Toroid_Vertical_L46.0mm_W19.1mm_P21.80mm_Bourns_5700; Manufacturer Part Number HF400-601M-8.0AV; JLCPCB BOM 0
LED401, LED402: 9V (Green); LED_0805_2012Metric; Manufacturer Part Number APTD2012LCGCK; JLCPCB BOM 0
Q401, Q402: NMOS; TO-247-3_Vertical; Manufacturer Part Number IXFH80N65X2; JLCPCB BOM 0
R401: 15k; R_0805_2012Metric; Manufacturer Part Number 0805W8F1502T5E; JLCPCB BOM 1
R402: 10k; R_0805_2012Metric; Manufacturer Part Number 0805W8F1002T5E; JLCPCB BOM 1
R403: R; TO-220-2_Vertical; Manufacturer Part Number PWR220T-35-33R0J; JLCPCB BOM 0
R404: 27k; R_0805_2012Metric; Manufacturer Part Number 0805W8F2702T5E; JLCPCB BOM 1
TP401: GATE; TestPoint_Pad_1.0x1.0mm
TP402: +SNUB; TestPoint_Pad_1.0x1.0mm
TP403: M_SNUB; TestPoint_Pad_1.0x1.0mm
TP404: -SNUB; TestPoint_Pad_1.0x1.0mm

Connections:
/+ARR: CP401.1, F401.1, L401.1, R401.1; also elsewhere on the board
/+BATT: CP402.1, D403.1 (K), D404.1 (K), F402.2, R404.1; also elsewhere on the board
/-ARR: J401.2 (-), LED401.1 (K); also elsewhere on the board
/-BATT: J402.2 (-), LED402.1 (K); also elsewhere on the board
/DRIVE_PWM: D401.1 (K), Q401.1 (G), Q402.1 (G), R402.1, TP401.1; also elsewhere on the board
GND: C401.2, CP401.2, CP402.2, D401.2 (A), Q401.3 (S), Q402.3 (S), R402.2, TP404.1; also elsewhere on the board
unnamed: C401.1, D402.1 (K), R403.2, TP403.1
unnamed: D402.2 (A), D403.2 (A), D404.2 (A), L401.2, Q401.2 (D), Q402.2 (D), R403.1, TP402.1
unnamed: F401.2, J401.1 (+)
unnamed: F402.1, J402.1 (+)
unnamed: LED401.2 (A), R401.2
unnamed: LED402.2 (A), R404.2

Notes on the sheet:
DC-DC Boost Converter
Array Voltage Sensor
HIGH CURRENT FLOWS THROUGH THIS LOOP.
R403, C401 are experimental and are through hole components with a range of values.
0-115V to 0-175V boost converter. Maximum 8A current flow.
0-8A
0-6A
Battery Current Sensor
Array Current Sensor
Battery Voltage Sensor
Snubber

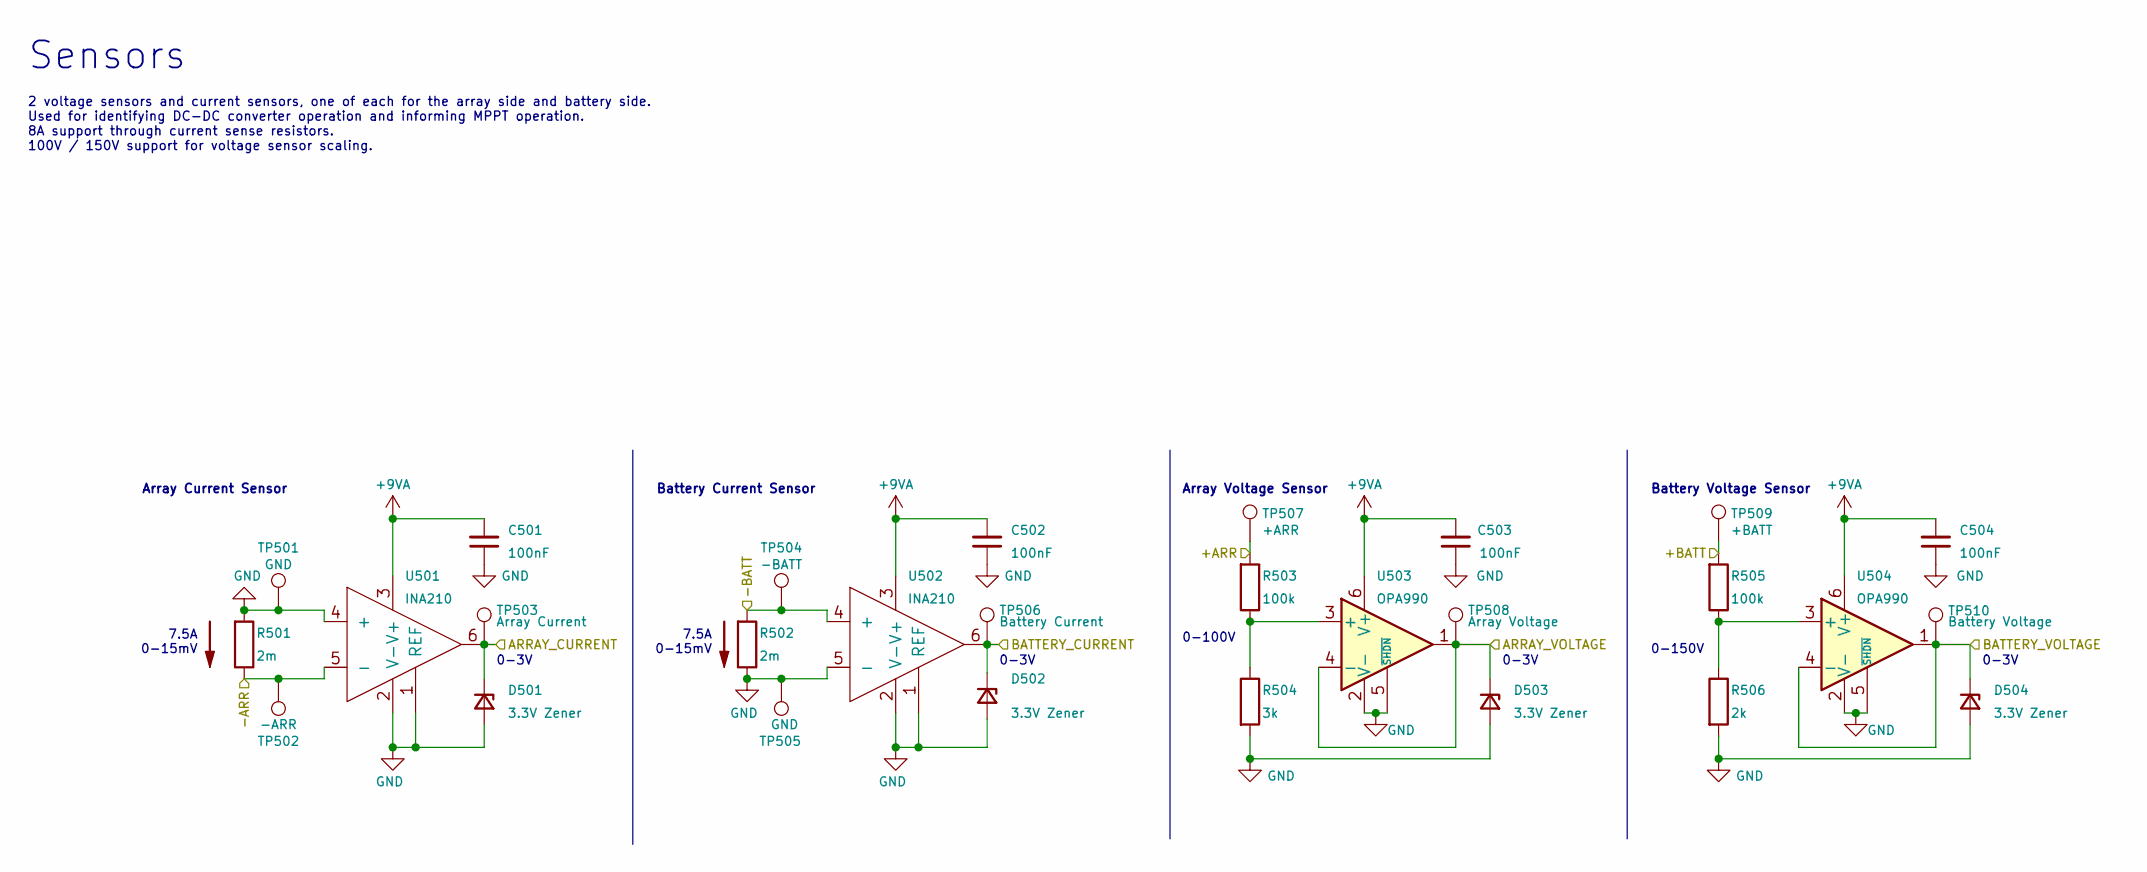
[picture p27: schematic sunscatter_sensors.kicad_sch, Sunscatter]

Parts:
C501, C502, C503, C504: 100nF; C_0805_2012Metric; Manufacturer Part Number CL21B104KCFNNNE; JLCPCB BOM 1
D501, D502, D503, D504: 3.3V Zener; D_MiniMELF; Manufacturer Part Number ZMM3V3-M; JLCPCB BOM 1
R501, R502: 2m; R_1206_3216Metric; Manufacturer Part Number PMR18EZPFV2L00; JLCPCB BOM 0
R503, R505: 100k; R_0805_2012Metric; Manufacturer Part Number 0805W8F1003T5E; JLCPCB BOM 1
R504: 3k; R_0805_2012Metric; Manufacturer Part Number 0805W8F3001T5E; JLCPCB BOM 1
R506: 2k; R_0805_2012Metric; Manufacturer Part Number 0805W8F2001T5E; JLCPCB BOM 1
TP501, TP505: GND; TestPoint_Pad_1.0x1.0mm
TP502: -ARR; TestPoint_Pad_1.0x1.0mm
TP503: Array Current; TestPoint_Pad_1.0x1.0mm
TP504: -BATT; TestPoint_Pad_1.0x1.0mm
TP506: Battery Current; TestPoint_Pad_1.0x1.0mm
TP507: +ARR; TestPoint_Pad_1.0x1.0mm
TP508: Array Voltage; TestPoint_Pad_1.0x1.0mm
TP509: +BATT; TestPoint_Pad_1.0x1.0mm
TP510: Battery Voltage; TestPoint_Pad_1.0x1.0mm
U501, U502: INA210; SOT-363_SC-70-6_Handsoldering; Manufacturer Part Number INA210AIDCKT; JLCPCB BOM 0
U503, U504: OPA990; SOT-23-6; Manufacturer Part Number OPA990SIDBVR; JLCPCB BOM 0

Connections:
+9VA: C501.2, C502.2, C503.2, C504.2, U501.3 (V+), U502.3 (V+), U503.6 (V+), U504.6 (V+); also elsewhere on the board
/+ARR: R503.2, TP507.1; also elsewhere on the board
/+BATT: R505.2, TP509.1; also elsewhere on the board
/-ARR: R501.1, TP502.1, U501.5 (-); also elsewhere on the board
/-BATT: R502.2, TP504.1, U502.4 (+); also elsewhere on the board
/ARRAY_CURRENT: D501.1 (K), TP503.1, U501.6; also elsewhere on the board
/ARRAY_VOLTAGE: D503.1 (K), TP508.1, U503.1, U503.4 (-); also elsewhere on the board
/BATTERY_CURRENT: D502.1 (K), TP506.1, U502.6; also elsewhere on the board
/BATTERY_VOLTAGE: D504.1 (K), TP510.1, U504.1, U504.4 (-); also elsewhere on the board
GND: C501.1, C502.1, C503.1, C504.1, D501.2 (A), D502.2 (A), D503.2 (A), D504.2 (A), R501.2, R502.1, R504.2, R506.2, TP501.1, TP505.1, U501.1 (REF), U501.2 (V-), U501.4 (+), U502.1 (REF), U502.2 (V-), U502.5 (-), U503.2 (V-), U503.5 (~SHDN), U504.2 (V-), U504.5 (~SHDN); also elsewhere on the board
unnamed: R503.1, R504.1, U503.3 (+)
unnamed: R505.1, R506.1, U504.3 (+)

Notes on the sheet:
0-3V
7.5A 0-15mV
Array Current Sensor
Array Voltage Sensor
0-150V
2 voltage sensors and current sensors, one of each for the array side and battery side. Used for identifying DC-DC converter operation and informing MPPT operation. 8A support through current sense resistors. 100V / 150V support for voltage sensor scaling.
Sensors
Battery Current Sensor
Battery Voltage Sensor
0-100V

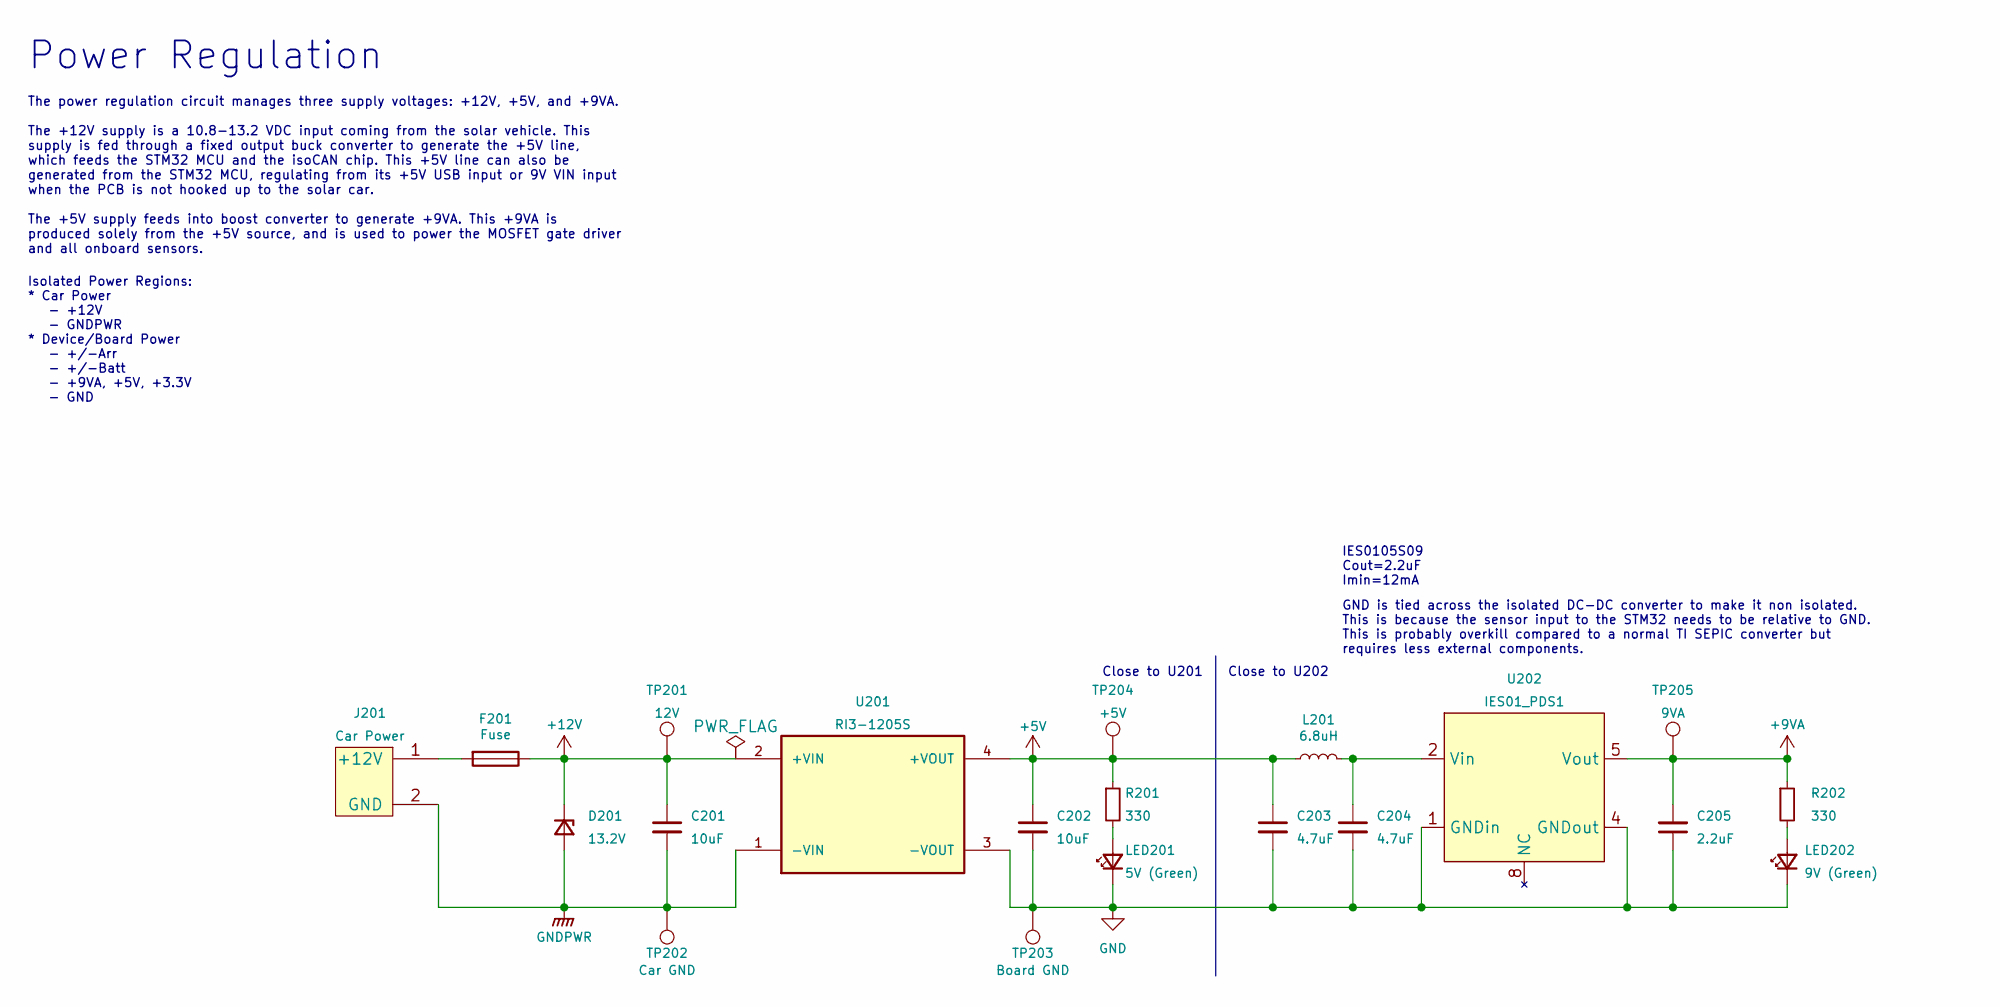
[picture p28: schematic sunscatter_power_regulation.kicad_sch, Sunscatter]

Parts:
C201, C202: 10uF; C_0805_2012Metric; Manufacturer Part Number CL21A106KAYNNNE; JLCPCB BOM 1
C203, C204: 4.7uF; C_0805_2012Metric; Manufacturer Part Number CL21A475KAQNNNE; JLCPCB BOM 1
C205: 2.2uF; C_0805_2012Metric; Manufacturer Part Number 0805F225M500NT; JLCPCB BOM 1
D201: 13.2V; D_SOD-323F; Manufacturer Part Number PZU13B2,115; JLCPCB BOM 0
F201: Fuse; 05200101Z_Fuze_Holder_5x20_PCB_Mount; Manufacturer Part Number 05200101Z; JLCPCB BOM 0
J201: Car Power; Molex_Micro-Fit_3.0_43650-0215_1x02_P3.00mm_Vertical; Manufacturer Part Number 43650-0215; JLCPCB BOM 0
L201: 6.8uH; L_Taiyo-Yuden_NR-50xx; Manufacturer Part Number NRS5040T6R8MMGJ; JLCPCB BOM 0
LED201: 5V (Green); LED_0805_2012Metric; Manufacturer Part Number APTD2012LCGCK; JLCPCB BOM 0
LED202: 9V (Green); LED_0805_2012Metric; Manufacturer Part Number APTD2012LCGCK; JLCPCB BOM 0
R201, R202: 330; R_0805_2012Metric; Manufacturer Part Number 0805W8F3300T5E; JLCPCB BOM 1
TP201: 12V; TestPoint_Pad_1.0x1.0mm
TP202: Car GND; TestPoint_Pad_1.0x1.0mm
TP203: Board GND; TestPoint_Pad_1.0x1.0mm
TP204: +5V; TestPoint_Pad_1.0x1.0mm
TP205: 9VA; TestPoint_Pad_1.0x1.0mm
U201: RI3-1205S; CONV_RI3-1205S; Manufacturer Part Number RI3-1205S; JLCPCB BOM 0
U202: IES01_PDS1; Manufacturer Part Number IES0105S09; JLCPCB BOM 0

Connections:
+5V: C202.1, C203.1, L201.1, R201.1, TP204.1, U201.4 (+VOUT); also elsewhere on the board
+9VA: C205.2, R202.1, TP205.1, U202.5 (Vout); also elsewhere on the board
+12V: C201.1, D201.1 (K), F201.1, TP201.1, U201.2 (+VIN)
GND: C202.2, C203.2, C204.2, C205.1, LED201.1 (K), LED202.1 (K), TP203.1, U201.3 (-VOUT), U202.1 (GNDin), U202.4 (GNDout); also elsewhere on the board
GNDPWR: C201.2, D201.2 (A), J201.2 (GND), TP202.1, U201.1 (-VIN)
unnamed: C204.1, L201.2, U202.2 (Vin)
unnamed: F201.2, J201.1 (+12V)
unnamed: LED201.2 (A), R201.2
unnamed: LED202.2 (A), R202.2

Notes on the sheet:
Close to U202
IES0105S09 Cout=2.2uF Imin=12mA
The power regulation circuit manages three supply voltages: +12V, +5V, and +9VA. The +12V supply is a 10.8-13.2 VDC input coming from the solar vehicle. This supply is fed through a fixed output buck converter to generate the +5V line, which feeds the STM32 MCU and the isoCAN chip. This +5V line ca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
Power Regulation
Isolated Power Regions: * Car Power - +12V - GNDPWR * Device/Board Power - +/-Arr - +/-Batt - +9VA, +5V, +3.3V - GND
Close to U201
GND is tied across the isolated DC-DC converter to make it non isolated. This is because the sensor input to the STM32 needs to be relative to GND. This is probably overkill compared to a normal TI SEPIC converter but requires less external components.

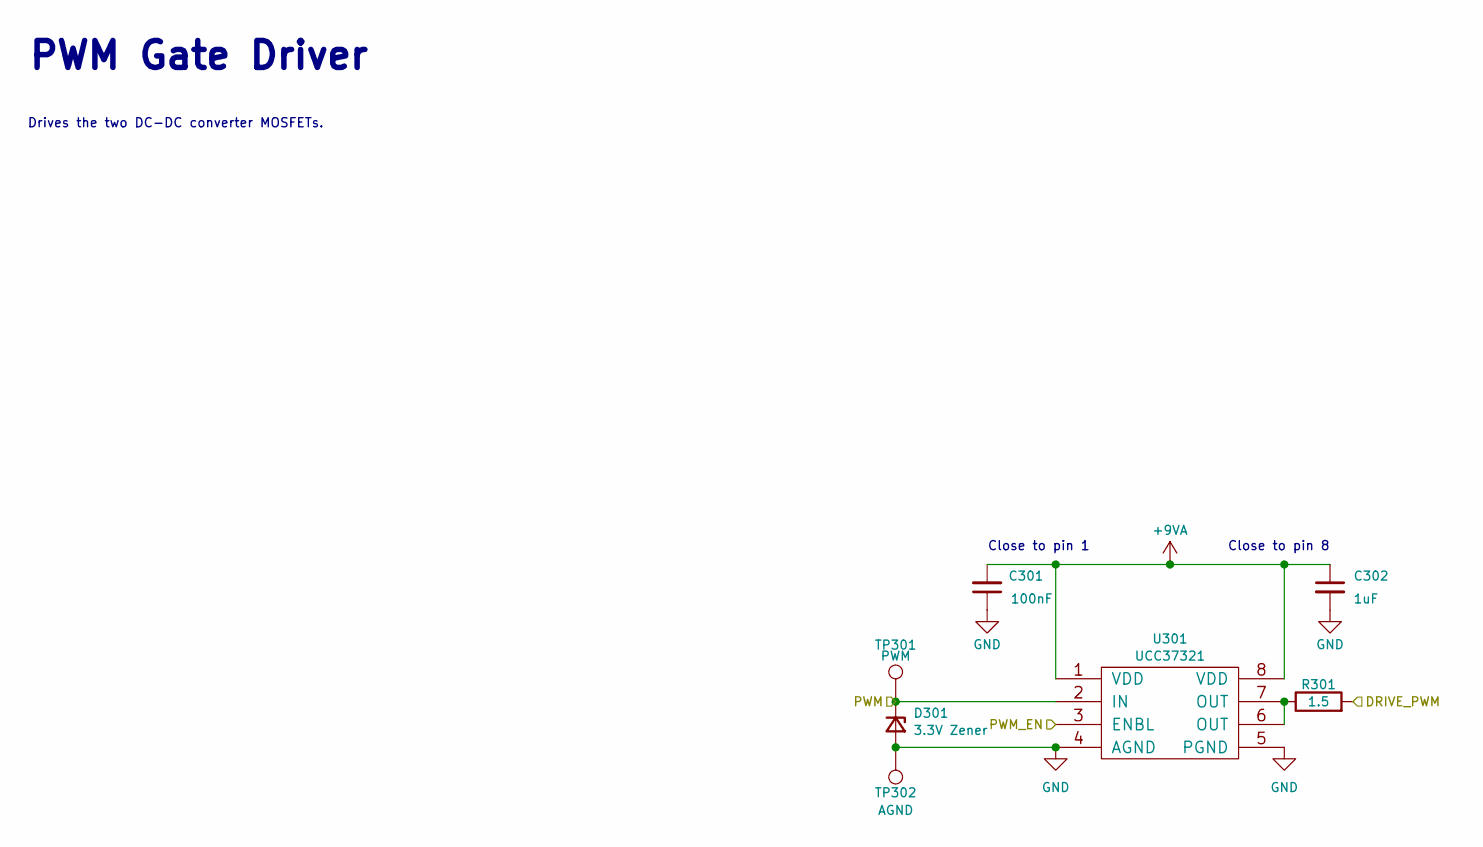
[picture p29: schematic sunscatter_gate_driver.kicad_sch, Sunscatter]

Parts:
C301: 100nF; C_0805_2012Metric; Manufacturer Part Number CL21B104KCFNNNE; JLCPCB BOM 1
C302: 1uF; C_0805_2012Metric; Manufacturer Part Number CL21B105KBFNNNE; JLCPCB BOM 1
D301: 3.3V Zener; D_MiniMELF; Manufacturer Part Number ZMM3V3-M; JLCPCB BOM 1
R301: 1.5; R_0805_2012Metric; Manufacturer Part Number CRCW08051R50FKEAHP; JLCPCB BOM 0
TP301: PWM; TestPoint_Pad_1.0x1.0mm
TP302: AGND; TestPoint_Pad_1.0x1.0mm
U301: UCC37321; SOIC-8_3.9x4.9mm_P1.27mm; Manufacturer Part Number UCC37321D; JLCPCB BOM 0

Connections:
+9VA: C301.2, C302.1, U301.1 (VDD), U301.8 (VDD); also elsewhere on the board
/DRIVE_PWM: R301.2; also elsewhere on the board
/PWM: D301.1 (K), TP301.1, U301.2 (IN); also elsewhere on the board
/PWM_EN: U301.3 (ENBL); also elsewhere on the board
GND: C301.1, C302.2, D301.2 (A), TP302.1, U301.4 (AGND), U301.5 (PGND); also elsewhere on the board
unnamed: R301.1, U301.6 (OUT), U301.7 (OUT)

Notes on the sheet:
Drives the two DC-DC converter MOSFETs.
Close to pin 1
PWM Gate Driver
Close to pin 8

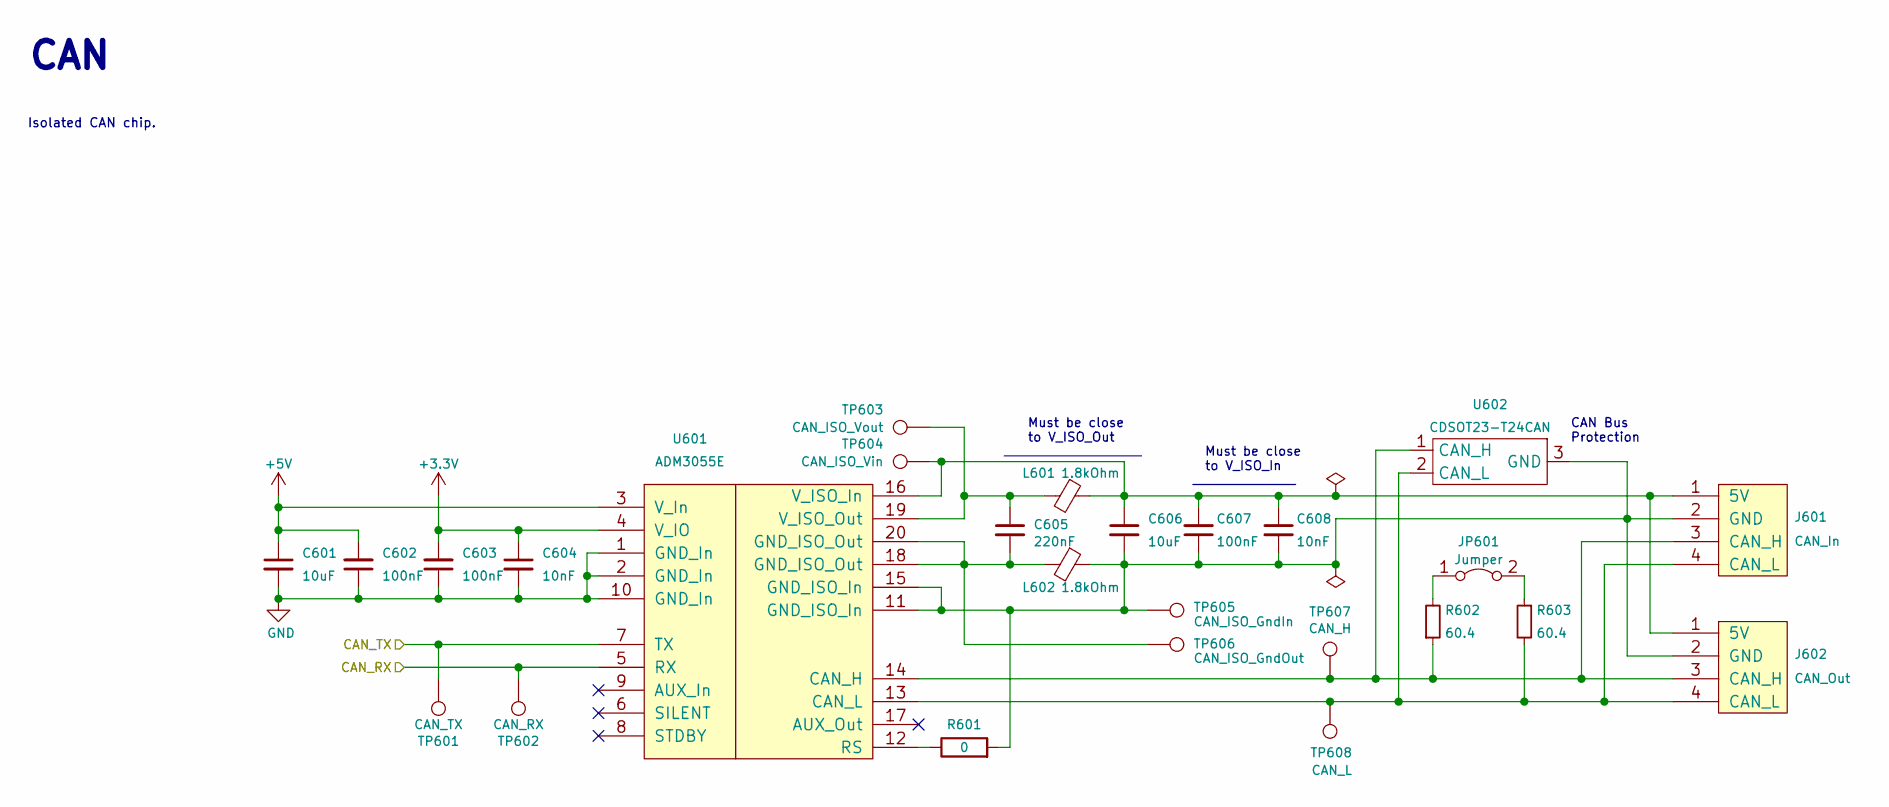
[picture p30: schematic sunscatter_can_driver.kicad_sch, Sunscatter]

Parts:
C601, C606: 10uF; C_0805_2012Metric; Manufacturer Part Number CL21A106KAYNNNE; JLCPCB BOM 1
C602, C603, C607: 100nF; C_0805_2012Metric; Manufacturer Part Number CL21B104KCFNNNE; JLCPCB BOM 1
C604, C608: 10nF; C_0805_2012Metric; Manufacturer Part Number CL21B103KBANNNC; JLCPCB BOM 1
C605: 220nF; C_0805_2012Metric; Manufacturer Part Number CL21B224KBFNNNE; JLCPCB BOM 1
J601: CAN_In; Molex_Micro-Fit_3.0_43650-0415_1x04_P3.00mm_Vertical; Manufacturer Part Number 43650-0427; JLCPCB BOM 0
J602: CAN_Out; Molex_Micro-Fit_3.0_43650-0415_1x04_P3.00mm_Vertical; Manufacturer Part Number 43650-0427; JLCPCB BOM 0
JP601: Jumper; PinHeader_1x02_P2.54mm_Vertical
L601, L602: 1.8kOhm; L_0805_2012Metric; Manufacturer Part Number BLM21BD182SN1D; JLCPCB BOM 0
R601: 0; R_0805_2012Metric; Manufacturer Part Number 0805W8F0000T5E; JLCPCB BOM 1
R602, R603: 60.4; R_0805_2012Metric; Manufacturer Part Number CRCW080560R4FKEAHP; JLCPCB BOM 0
TP601: CAN_TX; TestPoint_Pad_1.0x1.0mm
TP602: CAN_RX; TestPoint_Pad_1.0x1.0mm
TP603: CAN_ISO_Vout; TestPoint_Pad_1.0x1.0mm
TP604: CAN_ISO_Vin; TestPoint_Pad_1.0x1.0mm
TP605: CAN_ISO_GndIn; TestPoint_Pad_1.0x1.0mm
TP606: CAN_ISO_GndOut; TestPoint_Pad_1.0x1.0mm
TP607: CAN_H; TestPoint_Pad_1.0x1.0mm
TP608: CAN_L; TestPoint_Pad_1.0x1.0mm
U601: ADM3055E; ADM3055EBRIZ; Manufacturer Part Number ADM3055EBRIZ; JLCPCB BOM 0
U602: CDSOT23-T24CAN; SOT-23; Manufacturer Part Number CDSOT23-T24CAN-Q; JLCPCB BOM 0

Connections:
+5V: C601.1, C602.2, U601.3 (V_In); also elsewhere on the board
/CAN_RX: TP602.1, U601.5 (RX); also elsewhere on the board
/CAN_TX: TP601.1, U601.7 (TX); also elsewhere on the board
GND: C601.2, C602.1, C603.1, C604.2, U601.1 (GND_In), U601.2 (GND_In), U601.10 (GND_In); also elsewhere on the board
unnamed: C605.1, L601.2, TP603.1, U601.19 (V_ISO_Out)
unnamed: C605.2, L602.2, TP606.1, U601.18 (GND_ISO_Out), U601.20 (GND_ISO_Out)
unnamed: C606.1, C607.2, C608.1, J601.1 (5V), J602.1 (5V), L601.1, TP604.1, U601.16 (V_ISO_In)
unnamed: C606.2, C607.1, C608.2, J601.2 (GND), J602.2 (GND), L602.1, R601.2, TP605.1, U601.11 (GND_ISO_In), U601.15 (GND_ISO_In), U602.3 (GND)
unnamed: J601.3 (CAN_H), J602.3 (CAN_H), R602.1, TP607.1, U601.14 (CAN_H), U602.1 (CAN_H)
unnamed: J601.4 (CAN_L), J602.4 (CAN_L), R603.2, TP608.1, U601.13 (CAN_L), U602.2 (CAN_L)
unnamed: JP601.1 (A), R602.2
unnamed: JP601.2 (B), R603.1
unnamed: R601.1, U601.12 (RS)

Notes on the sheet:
CAN Bus Protection
CAN
Must be close to V_ISO_Out
Isolated CAN chip.
Must be close to V_ISO_In

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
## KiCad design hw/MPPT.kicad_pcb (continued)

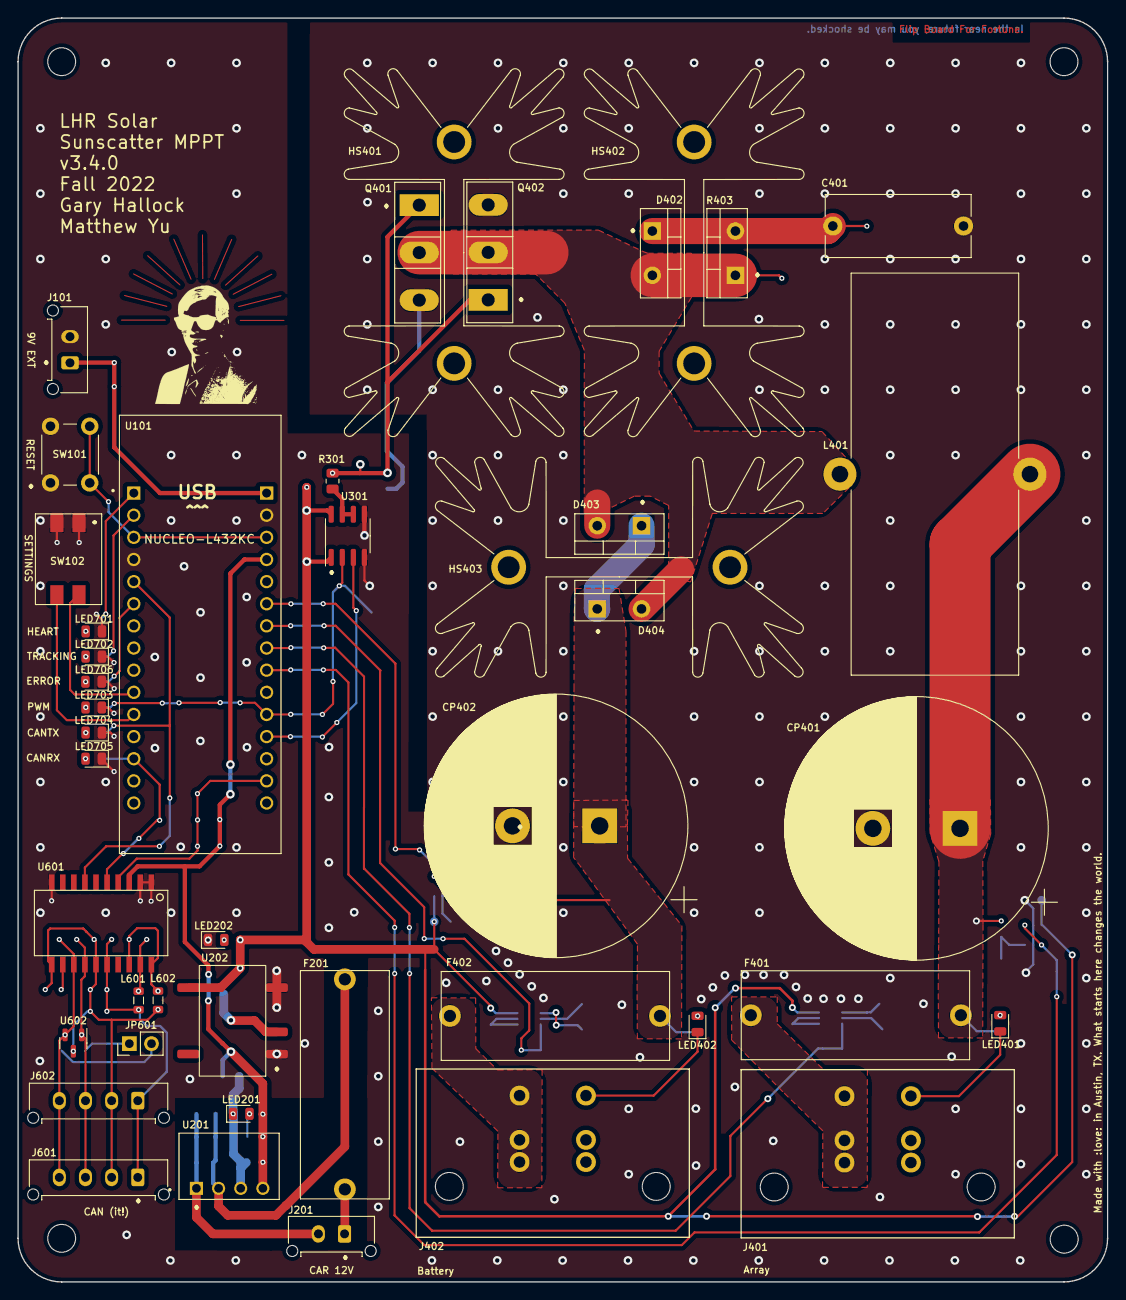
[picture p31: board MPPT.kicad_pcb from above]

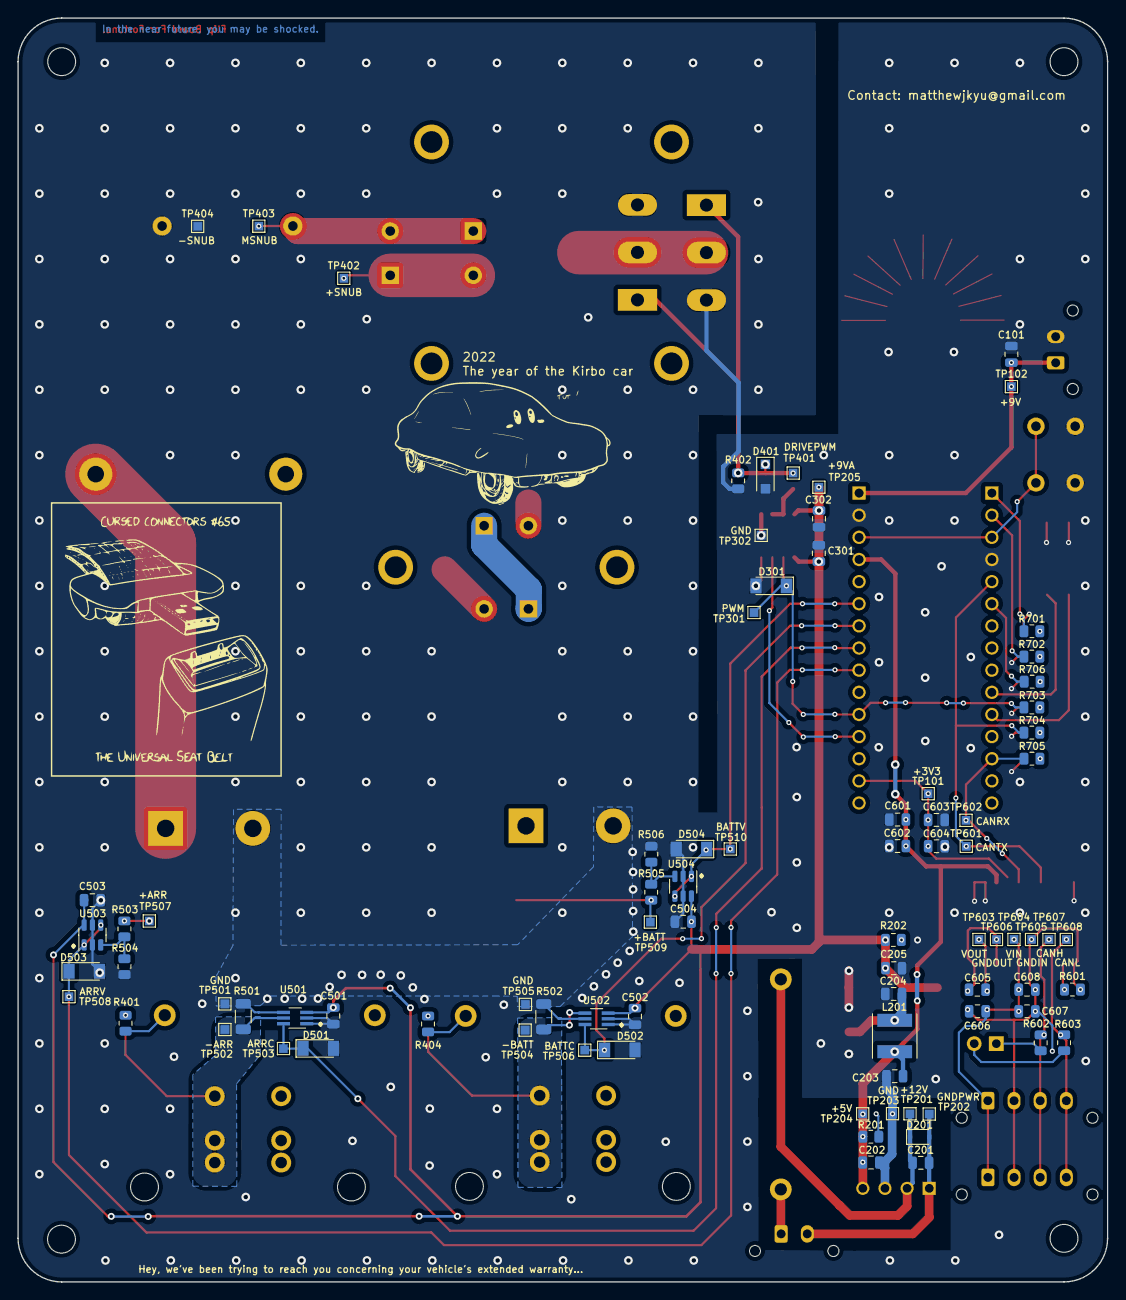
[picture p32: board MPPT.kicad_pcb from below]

Board: 2 copper layers, 125.0 x 145.0 mm, 131 parts (83 on the bottom side), 54 nets.

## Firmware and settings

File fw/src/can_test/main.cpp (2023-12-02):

/**
 * @file main.cpp
 * @author Matthew Yu (matthewjkyu@gmail.com) and Roy Mor (roymor.102@gmail.com)
 * @brief Test main that tests the CAN hardware on the v3.3.0 MPPTs.
 * @version 1.2.0
 * @date 2023-11-18
 * @copyright Copyright (c) 2022
 * @note Leave _LOOPBACK__ commented in to do loopback mode. Leave __USER_ONE__
 * commented in to transmit can_id = 0x0. Comment __USER_ONE__ out to transmit
 * can_id = 0x01.
 */
#include "mbed.h"
#include <cstdio>

#define PCB_MAJOR_VERSION   3
#define PCB_MINOR_VERSION   3
#define PCB_PATCH_VERSION   1
#define BLINKING_RATE       500ms
#define __LOOPBACK__        0
#define __USER_ONE__        0
#define CAN_SCA_ARR_VOLT 0x601
#define CAN_SCA_OVERRIDE 0x605
#define CAN_BBA_TEMP     0x626
#define CAN_BBA_IRRAD    0x627


Ticker ticker;
CAN can(D10, D2);           // D2 (TX), D10 (RX)
DigitalOut led(D13);        // STM32 Onboard LED
char counter = 0;
bool flag = false;
float temp_counter;


/**
 * @brief Tell the main thread to send a message and toggle the LED.
 */
void send() {
    led = !led;
    temp_counter += .5;
    if (!flag) {
        flag = true;
    }
}

/**
 * @brief Communicate with itself or another PCB via CAN.
 * 
 * @return int 
 */
int main() {
    ticker.attach(&send, 200000us);
    CANMessage msg;
    float volt = 5.712;
    float temp = 23.8;
    float irrad = 1000.0;
    temp_counter = 0;


#ifdef __LOOPBACK__
    can.mode(CAN::LocalTest);
#endif

#ifdef __USER_ONE__
    const uint32_t can_id = 0x00;
#else
    const uint32_t can_id = 0x01;
#endif

    while (true) {
        if (flag) {
            flag = false;
            //Sims MPPT 1-3 Setpoint & Measurement writing
            for(int i = 0; i < 15; i++) {
                can.write(CANMessage(CAN_SCA_ARR_VOLT, (char*)&volt, 4));
                printf("%f ", volt);
            }
            printf("\n");

            //Sims Blackbody A IRRAD writing
            for(int i = 0; i < 4; i++) {
                can.write(CANMessage(CAN_BBA_IRRAD, (char*)&irrad, 5));
                printf("%f ", irrad);
            }
            printf("\n");



            // if (can.write(CANMessage(can_id, &counter, 1))) {
            //     ++counter;
            //     printf("User %i sent message: %d\n", can_id, counter);
            // } else {
            //     printf("No message sent.\n");
            // }
        }

        //Sims Blackbody A TEMP writing
        if(temp_counter == 2.5) {
            temp_counter = 0;
            for(int i = 0; i < 8; i++) {
                can.write(CANMessage(CAN_BBA_TEMP, (char*)&temp, 5));
            }
        }

        if (can.read(msg)) {
            // printf("Message received from %i: %d\n", msg.id, msg.data[0]);
            if(msg.id == CAN_SCA_OVERRIDE) printf("RECEIVED OVERRIDE WOOOOOO, value = %d\n", msg.data[0]);
        } else {
            // printf("No message received.\n");
            ThisThread::sleep_for(100ms);
        }
    }

    return 0;
}

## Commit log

2020-08-02 Set up for own repo
    [BOM.csv, BPS-Nucleo.kicad_pcb, BPS-Nucleo.sch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]
2020-12-14 Major MPPT Board overhaul. Schematic advanced to Rev 3.2. Layout advanced to Rev 1.3. README and documentation updated. Parts list synchronized, standardized, and referenced.
    [MPPT-B_Cu.gbl, MPPT-B_Mask.gbs, MPPT-B_SilkS.gbo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]
2020-12-18 Addressed review.
    [MPPT.kicad_pcb]
2021-01-14 minor fixes and step rebuild.
    [MPPT-B_Cu.gbl, MPPT-B_Mask.gbs, MPPT-B_SilkS.gbo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]
2021-02-13 Rotated user comments on the layout and added PDFs of the version schematic and layout.
    [MPPT.kicad_pcb]
2022-02-04 schematic and layout revision.
    [MPPT-B_Cu.gbl, MPPT-B_Cu.gbr, MPPT-B_Mask.gbr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]
2022-02-04 secondary ground with via stitching
    [MPPT-B_Cu.gbr, MPPT-B_Mask.gbr, MPPT-B_Silkscreen.gbr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]
2022-02-11 Revisions on schematic and layout. See notes in the schematic for changes.
    [MPPT-B_Courtyard.gbr, MPPT-B_Cu.gbl, MPPT-B_Cu.gbr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]
2022-02-17 gerber rebuild for JLPCB errors
    [MPPT v3.3.0 BoM.xlsx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]
2022-04-01 gerber savestate
    [MPPT-B_Cu.gbr, MPPT-B_Mask.gbr, MPPT-B_Mask.gbs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]
2022-06-03 v3.3.1 changes.
    [MPPT.kicad_pcb, MPPT.kicad_sch]
2022-06-07 Version 3.4.0.
    Repo structure has significantly been updated for better navigation and exploration.
    Schematic has been broken into hierarchical sheets, all components have been reannotated.
    All schematic warnings have been expunged.
    Layout silkscreen has been updated to comply with new annotation.
    Datasheets for components have been added.
    ORDERING.md instructions have been updated. Now includes SMT/SMD assembly. And pictures.
    README.md is updated and simplified.
    IMPROVEMENT.md is extended.
    [MPPT v3.3.0 BoM.xlsx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]
2023-05-20 savestate 3.4.0
    [MPPT.kicad_pcb, MPPT.kicad_sch, sunscatter_boost_converter.kicad_sch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]
2023-05-20 restructuring, pulling in fw from power-gen repo
    [MPPT-CuBottom.gbr, MPPT-CuTop.gbr, MPPT-EdgeCuts.gbr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]
2023-07-17 pull in latest from main, hopefully no changes here
    [MPPT-CuBottom.gbr, MPPT-CuTop.gbr, MPPT-EdgeCuts.gbr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]
2023-11-18 Updated CAN test simulating can writes for 3 MPPTs, 8 RTDs, & 2 Irrad sensors
    For LV Integration
